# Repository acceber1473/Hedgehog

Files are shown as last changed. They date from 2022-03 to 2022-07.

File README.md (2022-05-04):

# Hedgehog Preservation Game
A game developed to educate general audience - and kids in particular - to the dangers hedgehogs are facing, and the importance of trying to preserve them. A detailed description of the game experience can be found in a document in this repository.

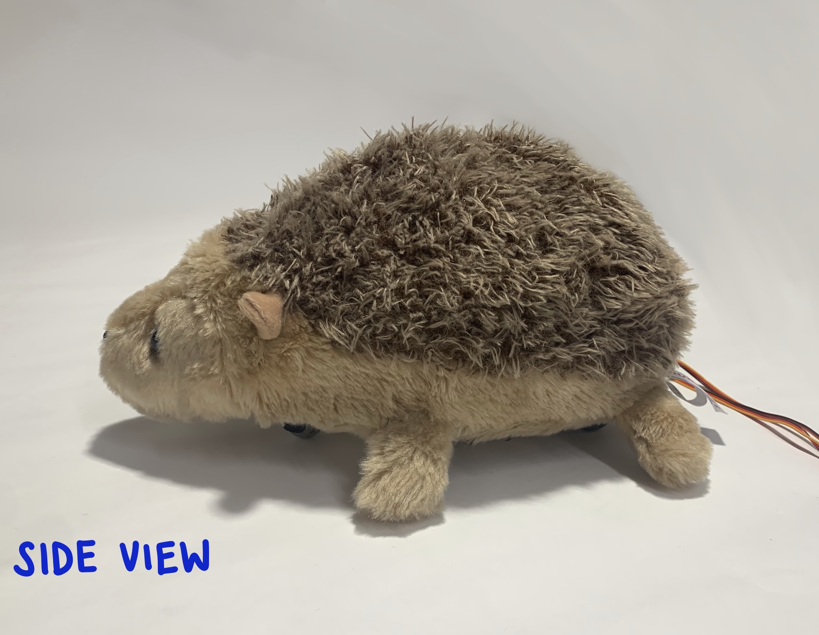
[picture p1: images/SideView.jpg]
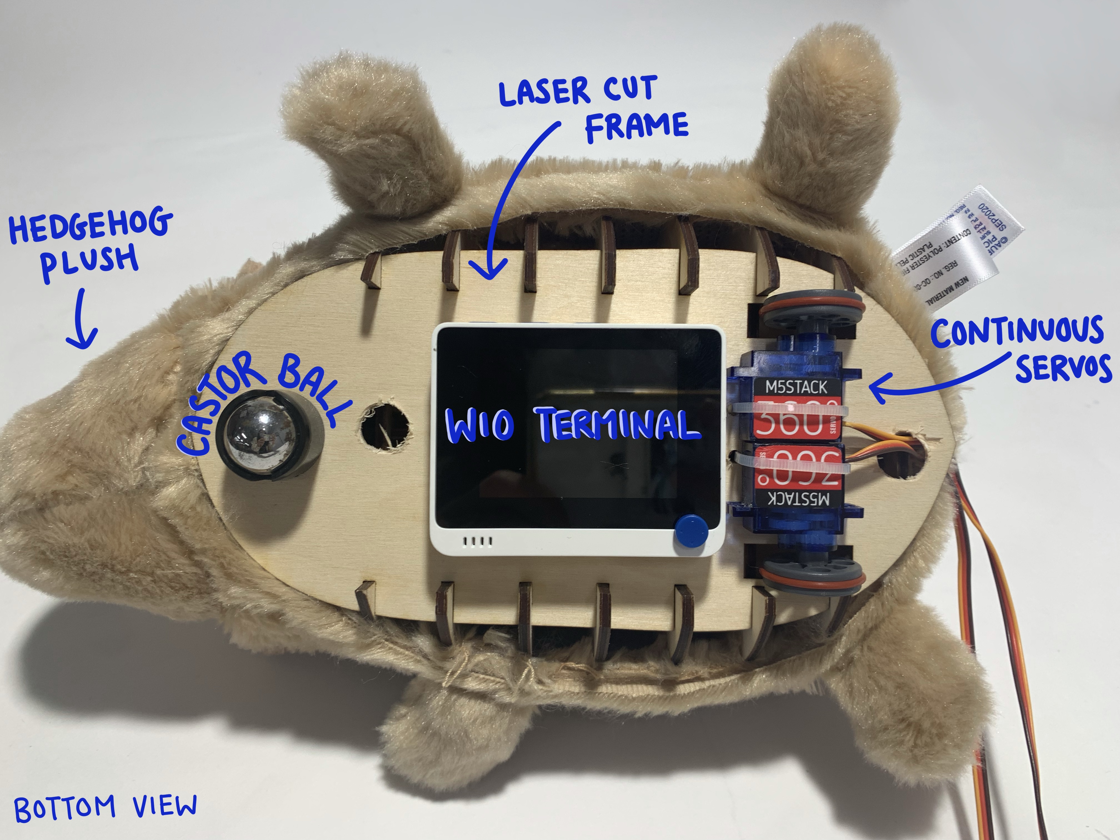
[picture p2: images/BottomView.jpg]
 

<p align = "center">
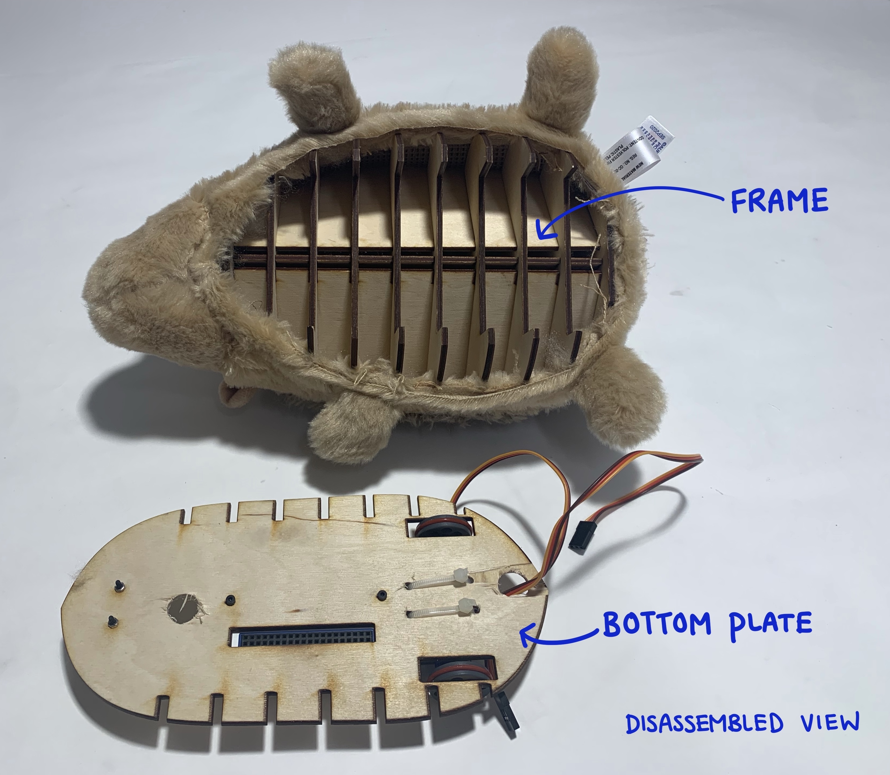
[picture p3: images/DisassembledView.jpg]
 
</p>

## Hardware 
This game is designed to be run on a Seeed WIO terminal and the following hardware is required:
* 1x - Seeed WIO terminal 
* 1x - WIO battery
* 2x - Continuous rotation servos (Either with grove port or grove adapter)
* 1x - Grove Multichannel V2 gas sensor
* 1x - Hedgehog stuffed toy
* 1x - Laser cut shell. Can be found in this repository

## Code Setup
* To run this code you must be running the latest WIO wifi firmware and download the associated libraries. The instructions for this update can be found here https://wiki.seeedstudio.com/Wio-Terminal-Network-Overview/
* The SAMD_ISR_Servo Library must be downloaded from here https://github.com/khoih-prog/SAMD_ISR_Servo. The patch mentioned in the readme file for the WIO terminal needs to be applied.
* Once the prerequisites are met, The Botv1.ino file can be opened in an Arduino IDE and uploaded to the board.
* For local KNN training, the Arduino_KNN library must be downloaded from https://www.arduino.cc/reference/en/libraries/arduino_knn/. The ZIP library can be uploaded on your local Arduino application. 
* For Edge Impulse, please follow this PDF with instructions to set up your own training module, or clone the existing module here. 

### This README is a work in progress ###

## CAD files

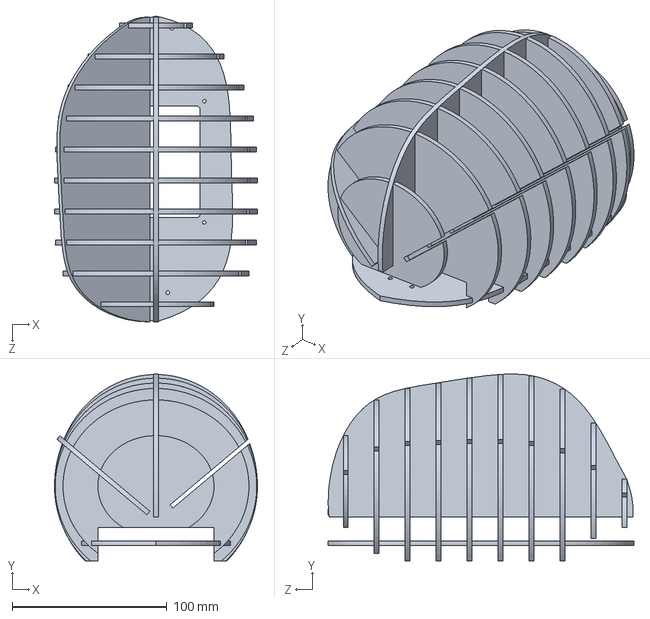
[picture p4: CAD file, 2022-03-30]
Laser cut shell/Solidworks Files/Laser cut Shell.SLDPRT
131.0 x 120.6 x 197.4 mm

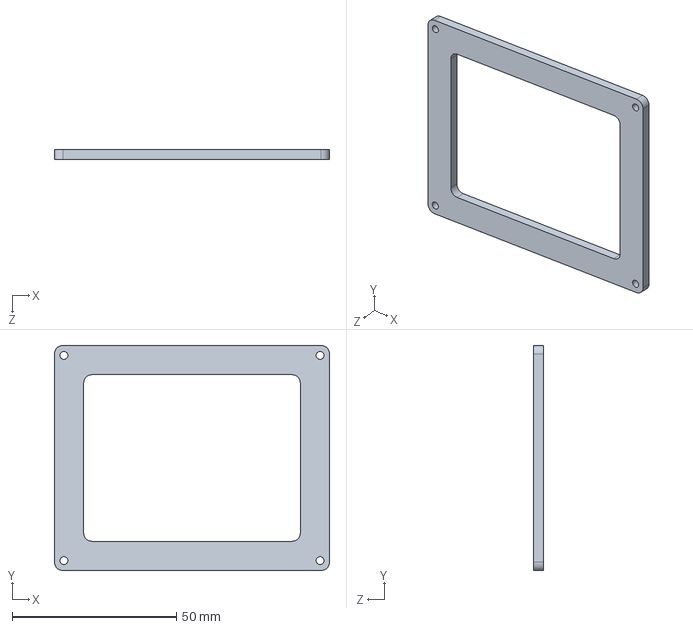
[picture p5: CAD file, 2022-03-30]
Laser cut shell/Solidworks Files/WIO plate.SLDPRT
83.8 x 68.6 x 3.00 mm

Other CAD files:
Laser cut shell/Individual DWG files/Left Rib.dwg
Laser cut shell/Individual DWG files/Plane 10.dwg
Laser cut shell/Individual DWG files/Plane 8.dwg
Laser cut shell/Individual DWG files/Plane 4.dwg
Laser cut shell/Individual DWG files/Plane 1.dwg
Laser cut shell/Individual DWG files/Bottom Plate.dwg
Laser cut shell/Individual DWG files/Plane 2.dwg
Laser cut shell/Individual DWG files/Right rib.dwg
Laser cut shell/Individual DWG files/WIO plate.dwg
Laser cut shell/Individual DWG files/Plane 3.dwg
Laser cut shell/Individual DWG files/Middle Rib.dwg
Laser cut shell/Individual DWG files/Plane 5.dwg
Laser cut shell/Individual DWG files/Plane 6.dwg
Laser cut shell/Individual DWG files/Plane 9.dwg
Laser cut shell/Individual DWG files/Plane 7.dwg

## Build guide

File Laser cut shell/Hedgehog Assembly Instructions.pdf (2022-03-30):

## Hedgehog Assembly Instructions

Last updated: 3/29/2022
The Hedgehog robot can be built out of a laser-cut shell. This is a structure with planes cut from the hedgehog cross-section with spines holding it together. Finally, a bottom plate is where the hardware can be mounted. A CAD model of this assembly with different views is shown below.

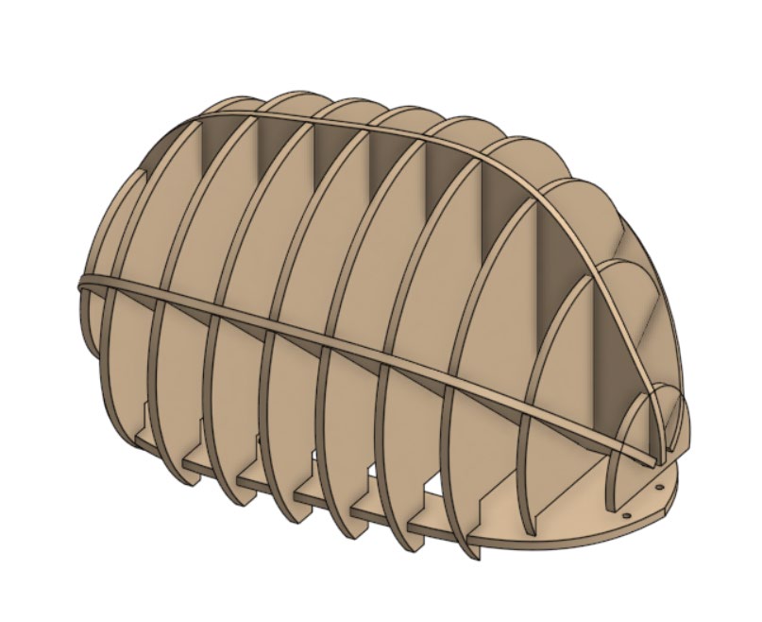
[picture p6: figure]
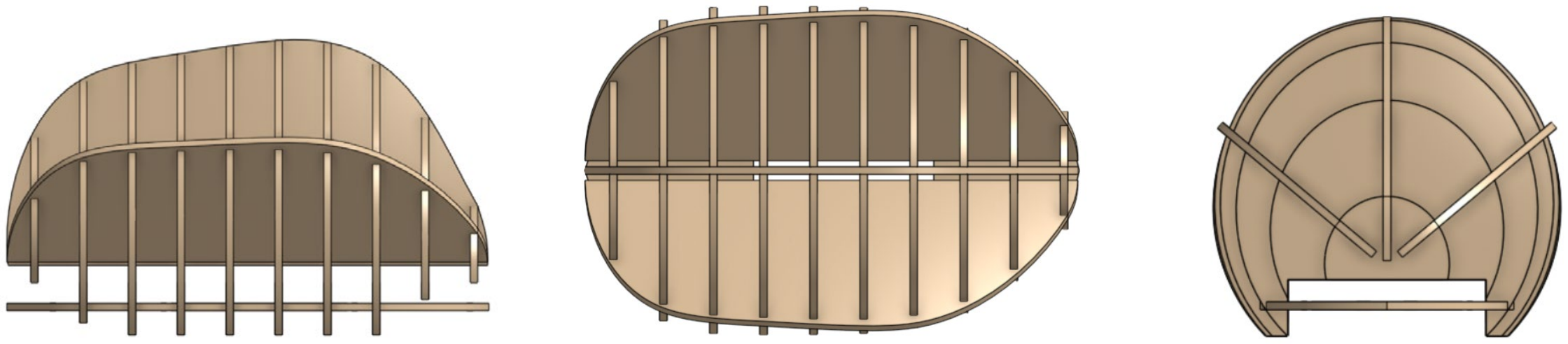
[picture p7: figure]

In order to make this structure each of the parts for laser cutting have been included in the github repo under Hedgehog/Laser cut shell/Individual DWG files. Additionally two illustrator files have been added under Hedgehog/Lasercut shell/Arranged Illustrator files. The illustrator files have all the components arranged on a 24x12in artboard for easy laser cutting.

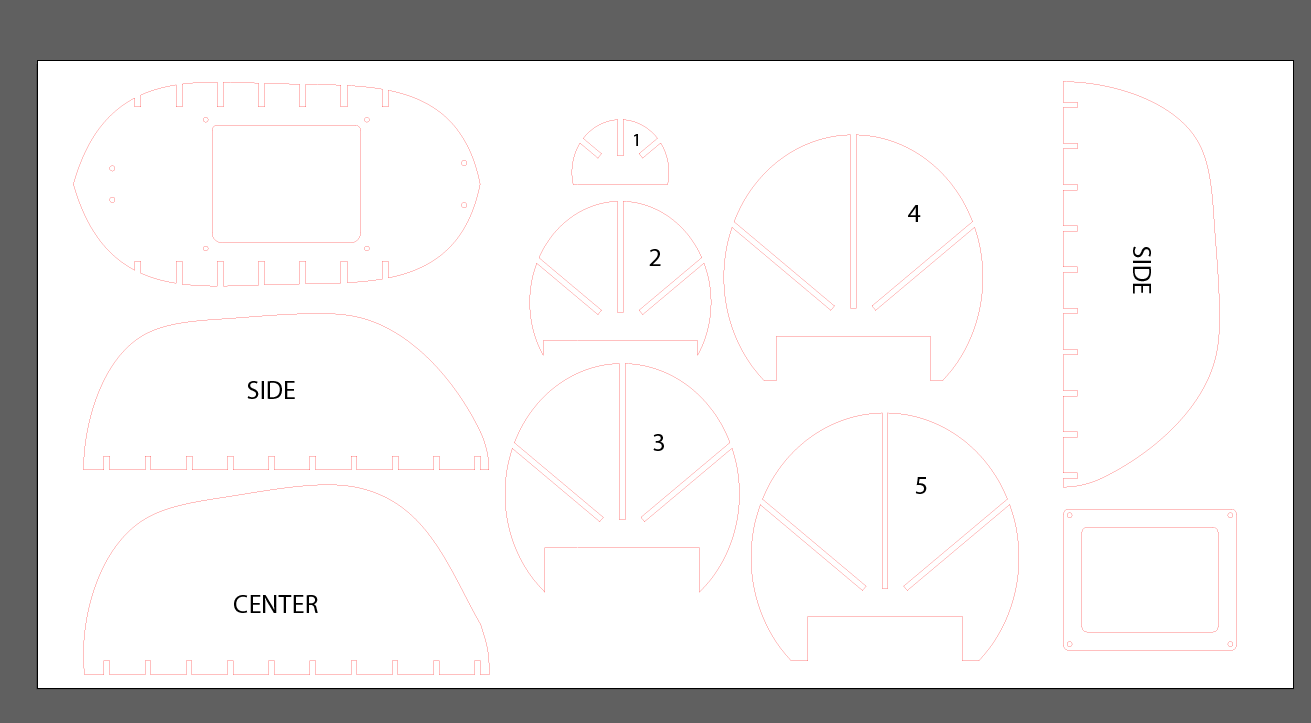
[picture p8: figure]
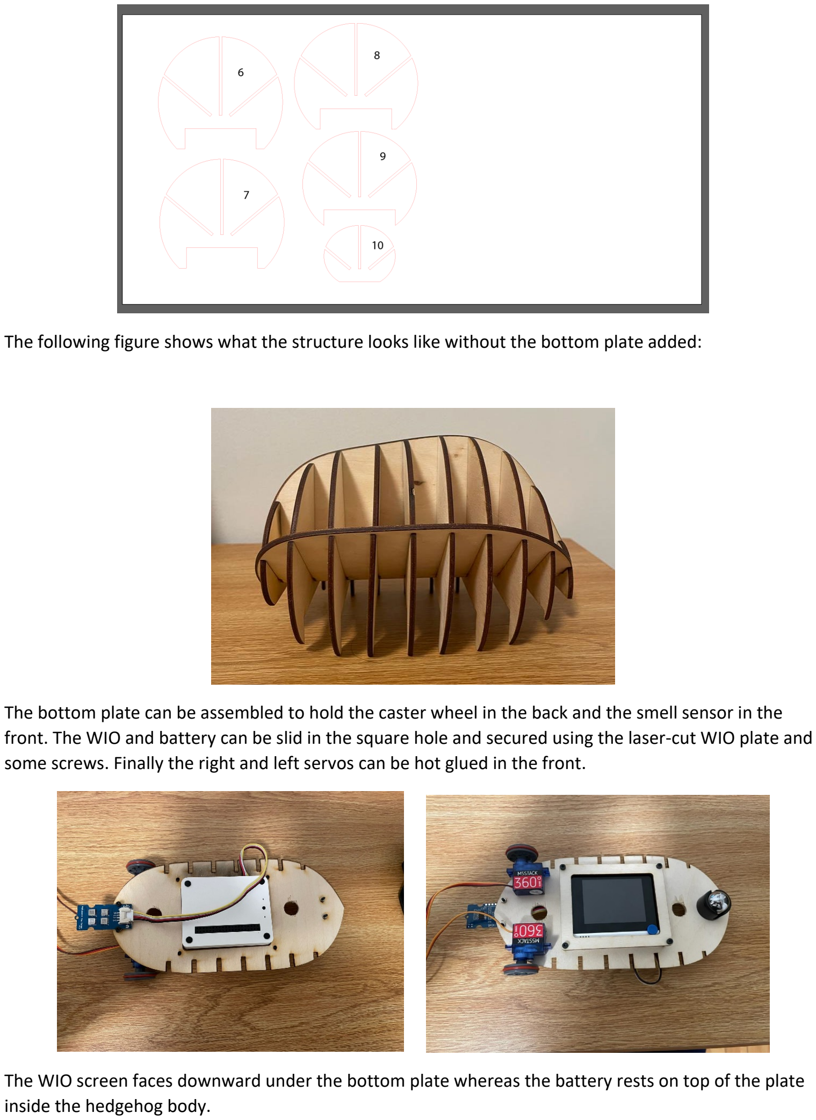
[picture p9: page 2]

The following figure shows what the structure looks like without the bottom plate added:

The bottom plate can be assembled to hold the caster wheel in the back and the smell sensor in the front. The WIO and battery can be slid in the square hole and secured using the laser-cut WIO plate and some screws. Finally the right and left servos can be hot glued in the front.

The WIO screen faces downward under the bottom plate whereas the battery rests on top of the plate inside the hedgehog body.

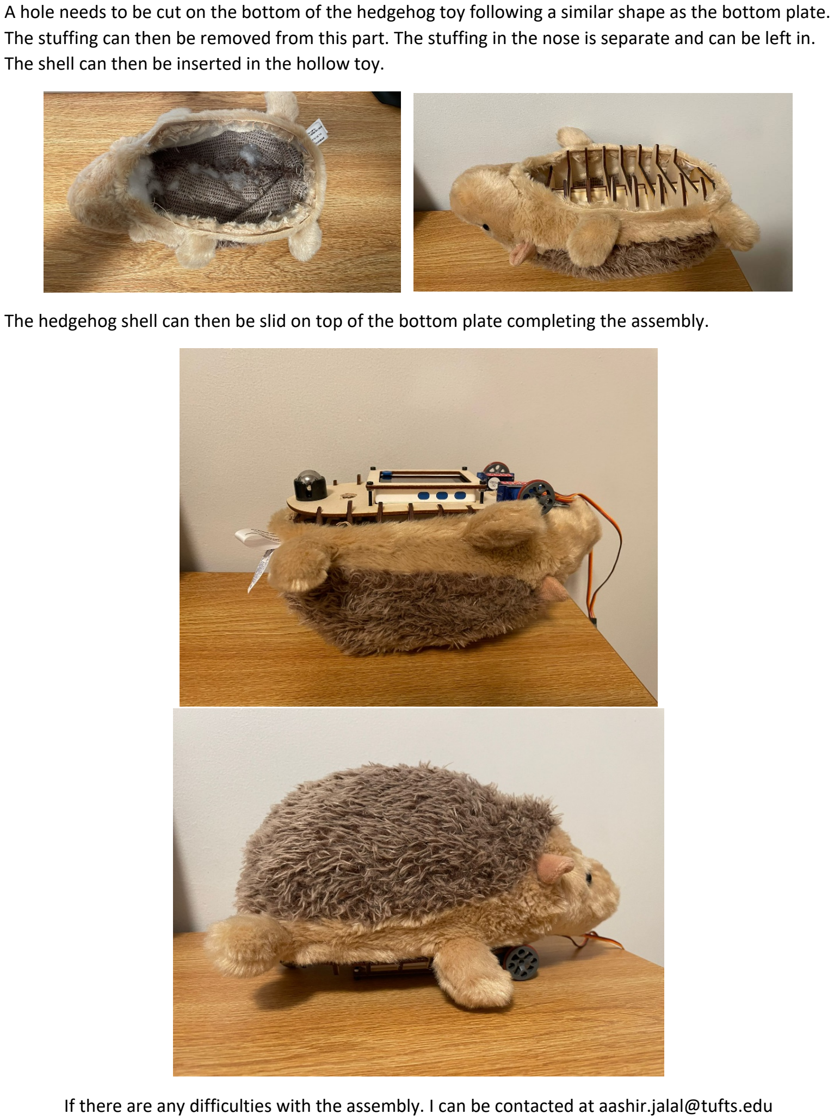
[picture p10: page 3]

A hole needs to be cut on the bottom of the hedgehog toy following a similar shape as the bottom plate. The stuffing can then be removed from this part. The stuffing in the nose is separate and can be left in. The shell can then be inserted in the hollow toy.

The hedgehog shell can then be slid on top of the bottom plate completing the assembly.

If there are any difficulties with the assembly. I can be contacted at aashir.jalal@tufts.edu

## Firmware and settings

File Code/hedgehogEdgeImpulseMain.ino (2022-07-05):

#include <Hedgehog_inferencing.h>
#include <rpcWiFi.h>
#include <Multichannel_Gas_GMXXX.h>
#include <Wire.h>
#include "SAMD_ISR_Servo.h"
#include "TFT_eSPI.h"



#define ISR_SERVO_DEBUG             1
#define USING_SAMD_TIMER            TIMER_TC3
#define MIN_MICROS        500
#define MAX_MICROS        2500 

#define SERVO_PIN_1       A5
#define SERVO_PIN_2       A3

TFT_eSPI tft;
GAS_GMXXX<TwoWire> gas;



String message = "Ready for Classification";
float features[EI_CLASSIFIER_DSP_INPUT_FRAME_SIZE];
static bool debug_nn = false; 


String webPage, header;

typedef struct
{
  int     servoIndex;
  uint8_t servoPin;
} ISR_servo_t;

#define NUM_SERVOS            2
ISR_servo_t ISR_servo[] =
{
  { -1, SERVO_PIN_1 }, { -1, SERVO_PIN_2 }
};



const char *ssid = "YourWiFiSSID";
const char *pass = "YourWiFiPass"; 
//Servo lServo;
//Servo rServo;
int pos = 0;


float no2 = 0;
float c2h5ch = 0;
float voc = 0;
float co = 0;

WiFiServer server(80);

int raw_feature_get_data(size_t offset, size_t length, float *out_ptr) {
    memcpy(out_ptr, features + offset, length * sizeof(float));
    return 0;
}

void setup()
{
  gas.begin(Wire, 0x08);
  
  tft.begin();
  tft.setRotation(3);
  tft.fillScreen(TFT_WHITE);
  tft.setTextColor(TFT_BLACK);          
  tft.setTextSize(2);
  tft.drawString("Initializing...", 30, 100);
  tft.drawString("Please Wait", 30, 120);
  

  pinMode(ISR_servo[0].servoPin, OUTPUT);
  pinMode(ISR_servo[1].servoPin, OUTPUT);
  digitalWrite(ISR_servo[0].servoPin, LOW);
  digitalWrite(ISR_servo[1].servoPin, LOW);

//  Serial.begin(115200); 
  
//  while (!Serial){
//  }
//  Serial.print(F("\nStarting SAMD_MultipleRandomServos on ")); Serial.println(BOARD_NAME);
//  Serial.println(SAMD_ISR_SERVO_VERSION);
  SAMD_ISR_Servos.useTimer(USING_SAMD_TIMER);
  
  for (int index = 0; index < NUM_SERVOS; index++)
  {
    ISR_servo[index].servoIndex = SAMD_ISR_Servos.setupServo(ISR_servo[index].servoPin, MIN_MICROS, MAX_MICROS);

    if (ISR_servo[index].servoIndex != -1)
    {
//      Serial.print(F("Setup OK Servo index = ")); Serial.println(ISR_servo[index].servoIndex);
    }
    else
    {
//      Serial.print(F("Setup Failed Servo index = ")); Serial.println(ISR_servo[index].servoIndex);
    }
  }

  SAMD_ISR_Servos.setReadyToRun();
  SAMD_ISR_Servos.setPosition(ISR_servo[0].servoIndex, 90);
  SAMD_ISR_Servos.setPosition(ISR_servo[1].servoIndex, 90 );
  

  delay(200);

  // We start by connecting to a WiFi network

//  Serial.println();
//  Serial.println();
//  Serial.print("Connecting to ");
//  Serial.println(ssid);

  WiFi.begin(ssid,pass);
  tft.drawString("Connecting WiFi", 30, 140);
  while (WiFi.status() != WL_CONNECTED)
  {
    delay(500);
//    Serial.print("Connecting to ");
//    Serial.println(ssid);
    WiFi.begin(ssid);
  }
  tft.setTextSize(2);
  tft.fillScreen(TFT_WHITE);
  tft.drawString("WiFi connected", 30, 100);

//  Serial.println("");
//  Serial.println("WiFi connected.");
//  Serial.println("IP address: ");
//  Serial.println(WiFi.localIP());
//  Serial.println(WiFi.macAddress());
//  Serial.println("Disabling Serial Connection");
//  Serial.end();
  server.begin();
  
  String ipString = WiFi.localIP().toString().c_str();
  tft.drawString(ipString, 30, 120);
  tft.drawString("Ready for Connection", 30, 140);    
}

int value = 0;


void printServoInfo(int indexServo)
{
  Serial.print(F("Servos idx = "));
  Serial.print(indexServo);
  Serial.print(F(", act. pos. (deg) = "));
  Serial.print(SAMD_ISR_Servos.getPosition(ISR_servo[indexServo].servoIndex) );
  Serial.print(F(", pulseWidth (us) = "));
  Serial.println(SAMD_ISR_Servos.getPulseWidth(ISR_servo[indexServo].servoIndex));
}

void loop()
{
  WiFiClient client = server.available(); // listen for incoming clients

   if (client) {
    boolean currLineIsBlank = true;
    while (client.connected()) 
    {
      if (client.available()) 
      {
        char c = client.read();
        header += c;        
        if (c == '\n' && currLineIsBlank) 
        {        

          if (header.indexOf("stop") != -1)
          {
            SAMD_ISR_Servos.setPosition(ISR_servo[0].servoIndex, 90 );
            SAMD_ISR_Servos.setPosition(ISR_servo[1].servoIndex, 90 );
            
          }
          
          else if (header.indexOf("classify") != -1)
          {
            for(int i=0;i<EI_CLASSIFIER_DSP_INPUT_FRAME_SIZE;i=i+4){
      
              features[i]=gas.getGM102B();  
              features[i+1] = gas.getGM302B();
              features[i+2]=gas.getGM502B();
              features[i+3]=gas.getGM702B();
      
              delay(EI_CLASSIFIER_INTERVAL_MS);
            }          
            ei_impulse_result_t result = { 0 };
            signal_t signal;
            numpy::signal_from_buffer(features, EI_CLASSIFIER_DSP_INPUT_FRAME_SIZE, &signal);
            String maxlabel;
            float maxval = 0;
            run_classifier(&signal, &result, debug_nn);
            for (size_t ix = 0; ix < EI_CLASSIFIER_LABEL_COUNT; ix++) {
              ei_printf("    %s: %.5f\n", result.classification[ix].label, result.classification[ix].value);
              if(result.classification[ix].value > maxval){
                maxval = result.classification[ix].value;
                maxlabel = result.classification[ix].label;
              }
             }
            message = "My guess is Class: " + maxlabel + " " + maxval;
          }
          
          else if (header.indexOf("message") != -1)
          {
            client.println(message);
            
          }
          else if (header.indexOf("forward") != -1)
          {
            SAMD_ISR_Servos.setPosition(ISR_servo[0].servoIndex, 0 );
            SAMD_ISR_Servos.setPosition(ISR_servo[1].servoIndex, 180 );
           
          }
           

          else if (header.indexOf("left") != -1)
          {
            SAMD_ISR_Servos.setPosition(ISR_servo[0].servoIndex, 0 );
            SAMD_ISR_Servos.setPosition(ISR_servo[1].servoIndex, 0 );


          }

          else if (header.indexOf("right") != -1)
          {
            SAMD_ISR_Servos.setPosition(ISR_servo[0].servoIndex, 180 );
            SAMD_ISR_Servos.setPosition(ISR_servo[1].servoIndex, 180 );
          }  

          else if (header.indexOf("back") != -1)
          {
            SAMD_ISR_Servos.setPosition(ISR_servo[0].servoIndex, 180 );
            SAMD_ISR_Servos.setPosition(ISR_servo[1].servoIndex, 0 );

          }

          else 
          {
            HTML_webpage();
            client.print(webPage);
          }  
//          Serial.print(header);
     
          header = "";
          break;
        }
        if (c =='\n') currLineIsBlank = true;
        else if(c != '\r') currLineIsBlank = false;
      }
    }
    client.stop();
  }
}

void HTML_webpage(){
  webPage = "HTTP/1.1 200 OK \n Content-Type:text/html \n \n";
  webPage += R"***(
  <!DOCTYPE HTML>
  <head><meta name="viewport" content="width=device-width, initial-scale=1">
  <link rel="icon" href="data:,">
  <html>
  <body style = "background-color:lightslategrey;font-family: Helvetica, sans-serif">
      <h1 style="text-align:center;color:white">Hedgehog Remote Control</h1>
      <table style="margin-left:auto;margin-right:auto;margin-top:auto;margin-bottom:auto;">
          <tr><td colspan="3" align="center"><button style="height:100px;width:150px" onmousedown="toggleCheckbox('forward');" ontouchstart="toggleCheckbox('forward');" onmouseup="toggleCheckbox('stop');" ontouchend="toggleCheckbox('stop');">Forward</button></td></tr>
          <tr><td align="center"><button style="height:100px;width:150px" onmousedown="toggleCheckbox('left');" ontouchstart="toggleCheckbox('left');" onmouseup="toggleCheckbox('stop');" ontouchend="toggleCheckbox('stop');">Left</button></td><td align="center"><button style="height:100px;width:100px" onmousedown="toggleCheckbox('stop');" ontouchstart="toggleCheckbox('stop');">Stop</button></td><td align="center"><button style="height:100px;width:150px" onmousedown="toggleCheckbox('right');" ontouchstart="toggleCheckbox('right');" onmouseup="toggleCheckbox('stop');" ontouchend="toggleCheckbox('stop');">Right</button></td></tr>
          <tr><td colspan="3" align="center"><button style="height:100px;width:150px" onmousedown="toggleCheckbox('backward');" ontouchstart="toggleCheckbox('backward');" onmouseup="toggleCheckbox('stop');" ontouchend="toggleCheckbox('stop');">Backward</button></td></tr>
      </table>
      <br>      
      <br><br>
      <table style="margin-left:auto;margin-right:auto;margin-top:auto;margin-bottom:auto;">
      <tr><td colspan="3" align="center"><button style="height:100px;width:150px" onmousedown="buttonDownClassify('');" ontouchstart="buttonDownClassify('');">Classify</button></td></tr>
      </table>
      <h3 style="text-align:center;color:white"><span id = "outputText" >Ready for Classification</span></h3> 
  <script>    
      function toggleCheckbox(x) 
      {
          var xhr = new XMLHttpRequest();
          xhr.open("GET", "/" + x, true);
          xhr.send();
      }

      function buttonDownClassify() 
      {
          var xhr = new XMLHttpRequest();
          xhr.open("GET", "/classify", true);
          xhr.send();
          setTimeout(getMessage(),1000);         
      }

      function getMessage() 
      {
          var messageReq = new XMLHttpRequest();
          messageReq.onreadystatechange = function()
          {
              if(this.readyState == 4 && this.status == 200)
              {
                  document.getElementById("outputText").innerHTML = this.responseText;
              }
          };
          messageReq.open("GET","/message",true);
          messageReq.send(); 
      }
          
  </script>
  </body>
  </html>
  )***";
}

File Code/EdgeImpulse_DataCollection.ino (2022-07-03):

#include <Multichannel_Gas_GMXXX.h>
#include <Wire.h>
GAS_GMXXX<TwoWire> gas;


void setup() {
  // put your setup code here, to run once:
  gas.begin(Wire, 0x08); // use the hardware I2C
  Serial.begin(115200);
}

void loop() {
  
  String NO2 = String(gas.getGM102B());
  String C2H = String(gas.getGM302B());
  String VOC = String(gas.getGM502B());
  String CO = String(gas.getGM702B());
  Serial.println(NO2+","+C2H+","+VOC+","+CO);

  delay(10);

  
}
